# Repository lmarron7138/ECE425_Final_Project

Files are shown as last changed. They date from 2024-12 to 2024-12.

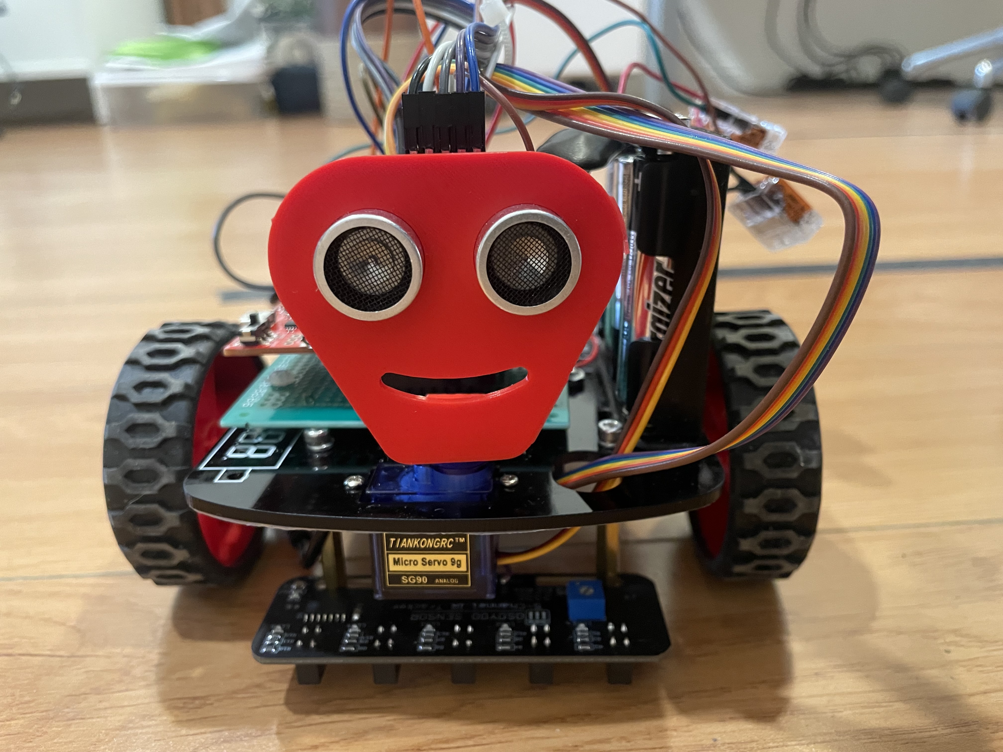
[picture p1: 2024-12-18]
Pictures/IMG_0241.JPG

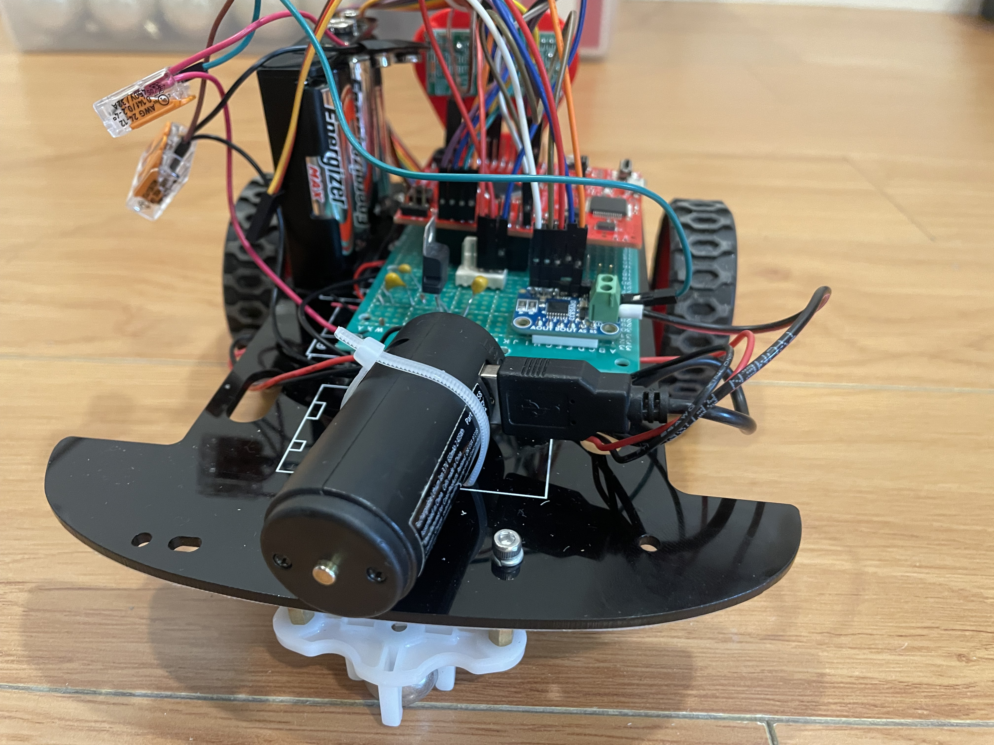
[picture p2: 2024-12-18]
Pictures/IMG_0248.JPG

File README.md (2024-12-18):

ECE 425 - Microprocessor Systems, Fall 2024

Final Project: Pathfinder Robot

Lenny Marron,
Roger Xu

Instructor: Aaron Nanas

## **<u>Introduction:</u>**

This project fulfills the final project requirement for the following
classes at California State University, Northridge (CSUN):

### **<u>Project Goals</u>**

To design and assemble a small robot that involves the use of an
ultrasonic sensor, and Two DC geared motors to give the robot the
ability to follow a specified path while avoiding
obstacles/obstructions. Using software written in C with Keil as the
development tool, the software instructions are sent to the TM4C123GXL
hardware board to process the data. This project explores data
transmission and communication protocols like UART, motor control with
PWM, Timer, and main microcontroller-peripherals interactions.

## **<u>Background and Methodology:</u>**

We used UART module 1 to transmit and receive the distance measured by
the ultrasonic sensor to the microcontroller and we used UART module 0
to allow us to view the data seen by the microcontroller. Once the data
was confirmed to be correct we then commented out the code relating to
UART module 0.

The DC motors were driven by the DRV8833 breakout board which used 4
separate PWM inputs to allow the robot to move forward, backward, left,
and right. We based our motor control using logic in **Table 1** below.

**<u>Table 1 Motor Control Logic</u>**



By using the DRV8833, it provided the ability to control 2 DC motors
with +3.3V input logic and a small footprint. The speed of the motors
was adjusted by changing the duty cycle of the PWM modules. When one
motor has a higher speed than the other, the car will turn in that
direction. When both motors have the same speed, the car will move
forward or backward.

Once the drivers for all 4 PWM signals and the 2 UART modules were
confirmed as working, a Timer Interrupt was created in order to
periodically check for any objects in front of the robots path. The
timer was set to count every 1 ms but would only check the distance in
front of it every 1 second. Whenever an object was less than 10 cm away
from the robot the robot would reverse and turn right, for all other
cases the robot would continue to drive forward.

We also 3D printed the ultrasonic sensor housing below in order to keep
the location of the US-100 sensor the same the entire time.

### **<u>CAD model of 3d Printed Parts</u>**

cad

## **<u>Block Diagram:</u>**



## **<u>Table of Components:</u>**

| **Part** | **QTY** | **Picture** |
|----|----|----|
| 5 Channel IR Tracking sensor module | 1 |  |
| DC Geared Motors with wires | 1 |  |
| Adafruit DRV8833 DC/Stepper Motor Driver Breakout Board | 1 |  |
| EK-TM4C123GXL microcontroller | 1 |  |
| US-100 Ultrasonic sensor | 1 |  |
| +6V (AA) battery Pack | 1 |  |
| +5V Coast Rechargeable Battery | 1 |  |

## 

## **<u>Pinout Table :</u>**

<table>
<colgroup>
<col style="width: 25%" />
<col style="width: 25%" />
<col style="width: 25%" />
<col style="width: 25%" />
</colgroup>
<thead>
<tr>
<th style="text-align: center;"><strong>EK-TM4C123GXL
Microcontroller</strong></th>
<th style="text-align: center;"><strong>Function Used</strong></th>
<th style="text-align: center;"><p><strong>DRV8833</strong></p>
<p><strong>Breakout Board</strong></p></th>
<th style="text-align: center;"><p><strong>US-100</strong></p>
<p><strong>Ultrasonic Sensor</strong></p></th>
</tr>
<tr>
<th style="text-align: center;">PB6</th>
<th style="text-align: center;"><p>PWM0_0</p>
<p>(Right motor forward)</p></th>
<th style="text-align: center;">BIN1</th>
<th style="text-align: center;"></th>
</tr>
<tr>
<th style="text-align: center;">PB4</th>
<th style="text-align: center;"><p>PWM0_1</p>
<p>(Right motor backward)</p></th>
<th style="text-align: center;">BIN2</th>
<th style="text-align: center;"></th>
</tr>
<tr>
<th style="text-align: center;">PF2</th>
<th style="text-align: center;"><p>PWM1_3</p>
<p>(Left motor forward)</p></th>
<th style="text-align: center;">AIN2</th>
<th style="text-align: center;"></th>
</tr>
<tr>
<th style="text-align: center;">PA6</th>
<th style="text-align: center;"><p>PWM1_1</p>
<p>(Left motor back)</p></th>
<th style="text-align: center;">AIN1</th>
<th style="text-align: center;"></th>
</tr>
<tr>
<th style="text-align: center;">PA0 (U0RX)</th>
<th style="text-align: center;">UART0</th>
<th style="text-align: center;"></th>
<th style="text-align: center;"></th>
</tr>
<tr>
<th style="text-align: center;">PA1 (U0TX)</th>
<th style="text-align: center;">UART0</th>
<th style="text-align: center;"></th>
<th style="text-align: center;"></th>
</tr>
<tr>
<th style="text-align: center;">PB0 (U1RX)</th>
<th style="text-align: center;">UART1</th>
<th style="text-align: center;"></th>
<th style="text-align: center;">Echo/RX pin 3</th>
</tr>
<tr>
<th style="text-align: center;">PB1 (U1TX)</th>
<th style="text-align: center;">UART1</th>
<th style="text-align: center;"></th>
<th style="text-align: center;">Trig/TX pin 2</th>
</tr>
</thead>
<tbody>
</tbody>
</table>

### **<u>Schematic:</u>**

()

## **<u>Analysis and Results :</u>**

One of the issues we ran into while working on this project was
implementing both the 5 channel IR tracking Sensors and the US-100
sensor at the same time. Although the interrupt function for the IR
sensor worked fine we always had errors when implementing both together.
Next time we will order an IR-sensor module that includes a datasheet
and comes from a reliable source. When troubleshooting this module using
a multimeter, we noticed the output voltages at ~ +1.7V when sensing the
black tape, which in turn caused the micro to read the input as a Logic
High, instead of Logic Low. We believe that if it weren’t due to the
lack of a datasheet we might have been able to fix this issue.

Another issue we faced is parsing the distance value measured by the
ultrasonic sensor to the microcontroller. We have had a lot of trouble
setting the microcontroller to measure the time it takes for the
ultrasonic sensor to receive its echo(which is how it measures
distance), we bypassed this issue by using UART as a communication
method instead of a direct pin connection. Aside from programming
obstacles, we have also experienced physical hardware roadblocks. The
ultrasonic sensor holder was not fitting properly, so we had to 3D print
new parts. However, despite all the setbacks, we were able to
successfully build a robot that scans its surroundings using sensors and
makes speed and direction changes based on its sensory inputs.

### **<u>Video Demonstration</u>**

Short video demonstration of collision avoidance:

- [<u>Video demo
  1</u>](https://drive.google.com/file/d/1N911rxExsTW1idhbEZjhIfGKM85qhewT/view?usp=drive_link)

- [<u>Video demo
  2</u>](https://drive.google.com/file/d/11KXWsSGZQswzX816z1DkIamCJ6btKC-2/view?usp=drive_link)

## **<u>Conclusion:</u>**

In conclusion, this project is the culmination of everything we have
learned in the class, from C programming to GPIO to GPTM to PWM to UART.
We connected different parts and peripherals to the microcontroller by
assigning and connecting them using GPIO pins. We applied communication
methods of UART to transfer distance data from the ultrasonic sensor to
the MCU by setting the appropriate baud rate. In addition we designed
the robot to periodically check its surroundings so as to not drain the
batteries as quickly. We learned how to use duty cycles to change the
speed of the motors by manipulating the duty cycle of the PWM, and thus
enabling us to adjust the speed of the motor. We also learned how to use
an H-bridge circuit to control the direction of our robot. We used
various C programming techniques to build up the control logic needed to
instruct the robot how to handle different situations. This project has
helped us gain a deeper understanding of MCUs and the crucial roles they
play in real life embedded systems.

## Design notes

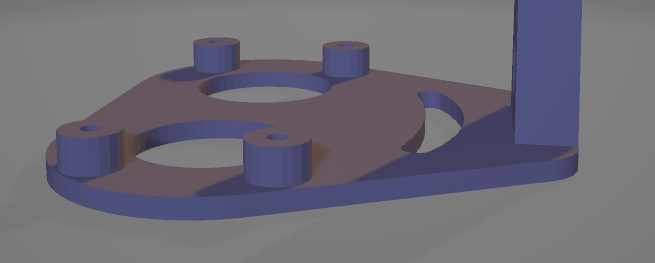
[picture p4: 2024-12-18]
3d_Models/Smiley Face ISO Left View.PNG

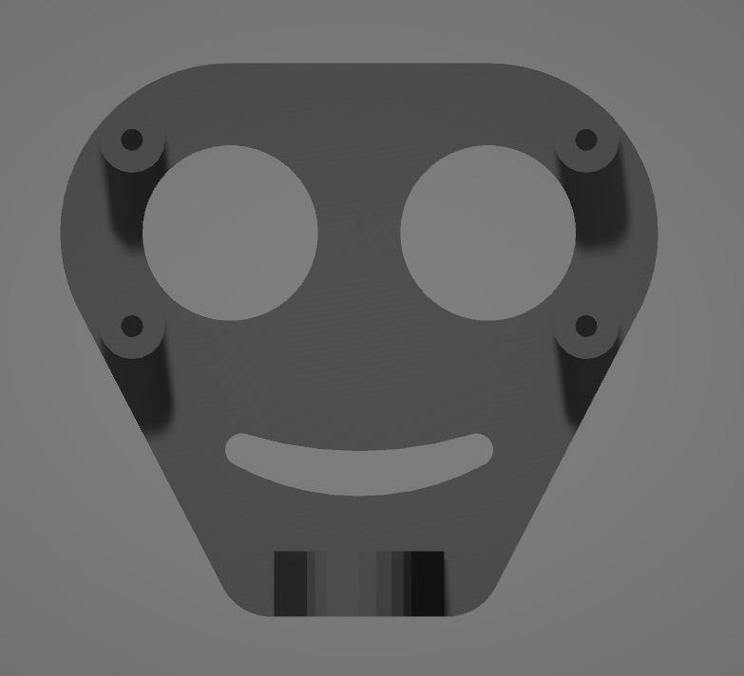
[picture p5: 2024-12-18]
3d_Models/Smiley Face Top View.PNG

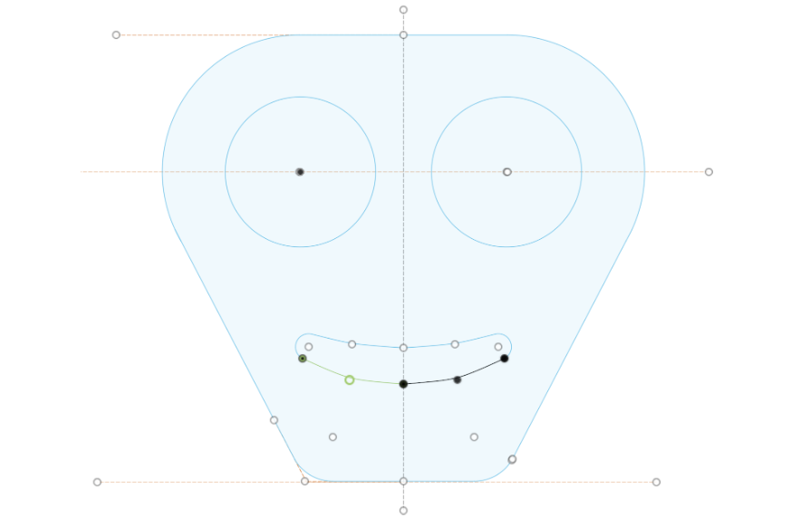
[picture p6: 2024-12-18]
3d_Models/Smiley Face Sketch.PNG

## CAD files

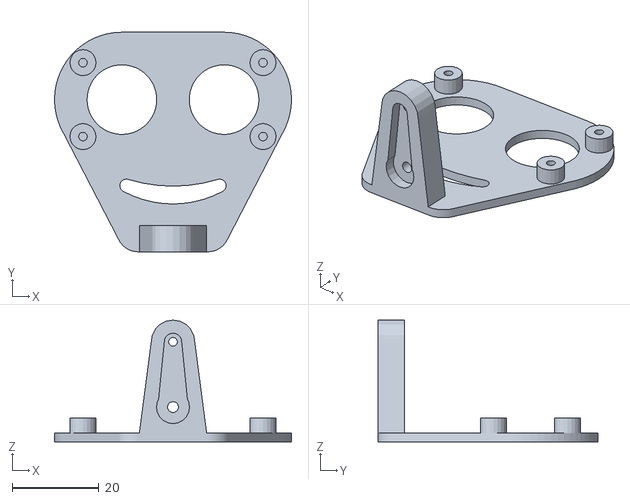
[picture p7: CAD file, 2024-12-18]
3d_Models/STL_Files/Smiley Face.stl
54.5 x 50.5 x 28.0

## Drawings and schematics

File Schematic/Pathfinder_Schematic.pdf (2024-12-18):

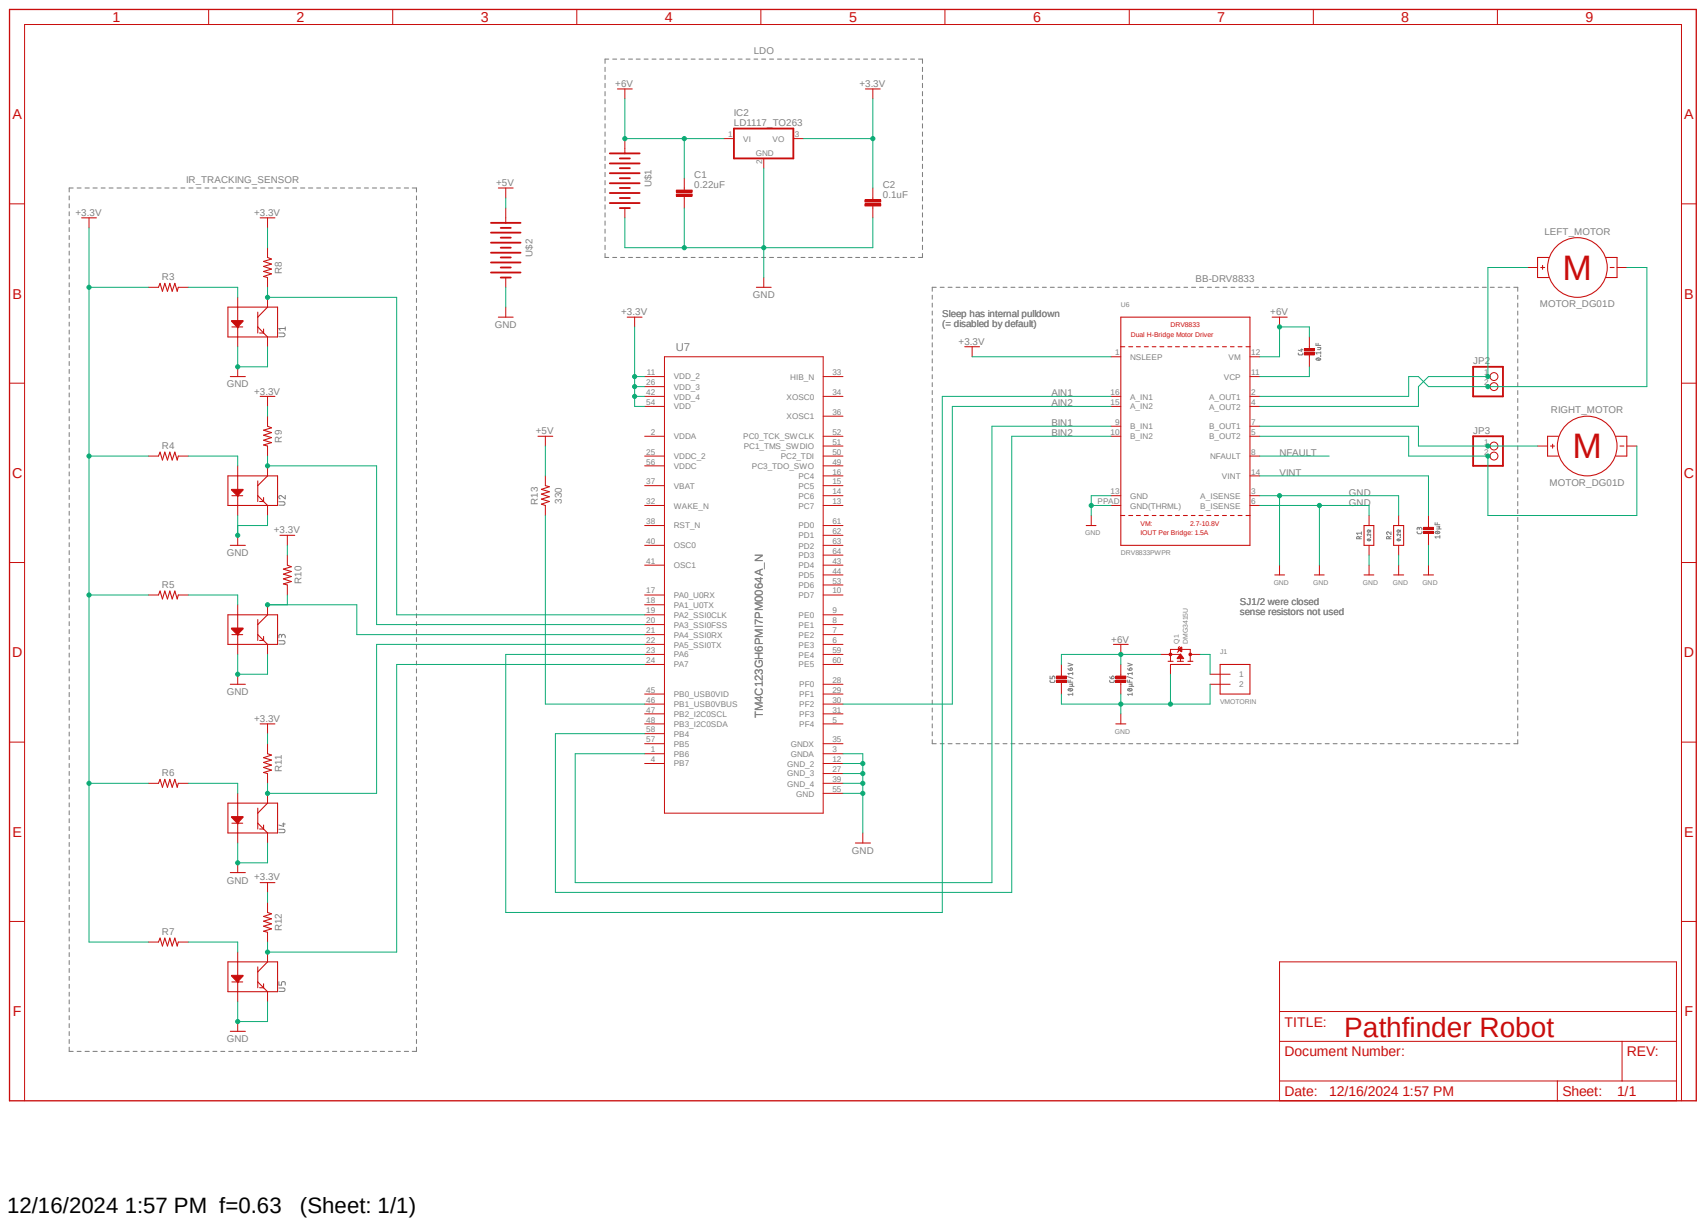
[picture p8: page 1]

Sleep has internal pulldown

SJ1/2 were closed
sense resistors not used

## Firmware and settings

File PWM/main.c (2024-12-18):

/*
 * @file main.c
 *
 * @brief Main source code for the Pathfinder Robot.
 *
 * This file contains the main entry point and function definitions for the Pathfinder Robot.
 * It Generates 4 PWM signals, a 1ms Timer interrupt, 9600 UART1 communication, SysTickTimer .
 *
 * Timer 0A generates periodic interrupts every 1 ms in order to count the 
 * amount of time needed to turn trigger the US-100 sensor and check obstacles in front of it. 
 *
 *
 * It interfaces with the following:
 *  - User LED (RGB) Tiva C Series TM4C123G LaunchPad
 *	- DRV8833 DC Motor Driver
 *	- SG90 Micro Servo Motor
 *	-	Two DC Motors Gearboxes 
 *				- Right motor controlled  PB6 (PWM0_0)FWD    PB4 (PWM0_1) REV
 *				- Left motor controlled   PF2 (PWM1_3)FWD    PA6 (PWM1_1) REV
 *
 *
 *	DRV8833 Breakout Board
 *  - DRV8833   (AIN1)  <-->  Tiva LaunchPad PA6
 *  - DRV8833   (AIN2)  <-->  Tiva LaunchPad PF2
 *  - DRV8833   (BIN1)  <-->  Tiva LaunchPad PB6
 *  - DRV8833   (BIN2)  <-->  Tiva LaunchPad PB4
 *  - DRV8833   (SLP)   <-->  +3.3V (Active High)
 *
 *  - DRV8833   (AOut1)<-->  DC Motor (+)
 *  - DRV8833   (AOut2)<-->  DC Motor (-)
 *  - DRV8833   (BOut2)<-->  DC Motor (-)
 *  - DRV8833   (BOut1)<-->  DC Motor (+)
 *
 *  - DRV8833   (VM+)  <-->  +6V (Battery Pack)
 *  - DRV8833   (VM-)  <-->  GND (Battery Pack)
 *
 * UART0 was used during the debugging
 * For PC communication using:
 *  - PA0 = UART0 RX
 *  - PA1 = UART0 TX
 *
 * The US-100 Ultrasonic Distance Sensor uses the following pinout:
 *  - US-100 Pin 1 (VCC)  <-->  Tiva LaunchPad 3.3V
 *  - US-100 Pin 2 (TX)   <-->  Tiva LaunchPad Pin PB1 (U1TX)
 *  - US-100 Pin 3 (RX)   <-->  Tiva LaunchPad Pin PB0 (U1RX)
 *  - US-100 Pin 4 (GND)  <-->  Tiva LaunchPad GND
 *  - US-100 Pin 5 (GND)  <-->  Tiva LaunchPad GND
 *
 *
 * @author Lenny Marron
 */
 

#include "TM4C123GH6PM.h"
#include "SysTick_Delay.h" 
#include "PWM_Clock.h"
#include "PWM0_0.h"
#include "PWM0_1.h"
#include "PWM1_1.h"
#include "PWM1_3.h"
#include "Motor_CTL.h"
#include "UART0.h"
#include "UART1.h"
#include "Timer_0A_Interrupt.h"
#include "IR_Tracking_Sensor_Interrupt.h"

#define BUFFER_SIZE   64
#define READ_DISTANCE 0x55

void Timer_0A_periodic_Task (void);
void IR_Sensor_Handler (uint8_t ir_sensor_status); //extern
static uint32_t Timer_0A_ms_elapsed= 0;
int Space  = 0;


int Distance_cm (void)
{
	char US_100_UART_Buffer[BUFFER_SIZE] = {0};
	
		UART1_Output_Character(READ_DISTANCE);
		
		US_100_UART_Buffer[0] = UART1_Input_Character();  //buffer aka read
		US_100_UART_Buffer[1] = UART1_Input_Character();
		
		uint16_t distance_value = ((US_100_UART_Buffer[1] | (US_100_UART_Buffer[0] << 8))/10);

	return distance_value ;
}



int main(void)
{
	//Used to Initialize Systick Timer blocking delay functions
	   SysTick_Delay_Init();
	
	// PWM clock divisor used to update clock to 3.125 MHz
	   PWM_Clock_Init();
	
	// Initializes PB and sets Period_Constant = 62500  
	   PWM0_0_Init(62500,0);  // works PB6
	
	// Initializes PB and sets Period_Constant = 62500  
     PWM0_1_Init(62500,0);  // works PB4
	
	// Initializes PB and sets Period_Constant = 62500   
     PWM1_1_Init(62500,0); // works PA6
	
	// Initializes PB and sets Period_Constant = 62500  
	   PWM1_3_Init(62500,0); // works PF2
	
	// Initialize the IR Channel Interrupts (Port A) 
	   //IR_Sensor_Interrupt_Init(&IR_Sensor_Handler); // working

  // Initialize the UART0 module which will be used to print characters on the serial terminal
	// UART0_Init();
	
	// Initialize the UART1 module which will be used to communicate with the US-100 Ultrasonic Distance Sensor
	   UART1_Init();
	
	// Initializes the Timer A0 Interrupts 
	   Timer_0A_Interrupt_Init (&Timer_0A_periodic_Task); //working
	
	while(1)
	{						
	    Move_FWD (0.3);
	}
}


// Timer will check distance every 1 seconds
void Timer_0A_periodic_Task (void)
{
	Timer_0A_ms_elapsed ++;
	
  if ((Timer_0A_ms_elapsed % 1000 ) == 0)
	{
	 Space = Distance_cm(); // measure distance infront
		 if (Space < 10)
		 {
			Move_Right (0.3);
			//SysTick_Delay1ms (200);
			 
			 // if (Space % 300)
			for (int i=0; i < 100; i++ )
			Move_REV ( .3 );    
     }
  }
}


/* 
******************************************
**  NOT WORKING WITH TIMER_0A and UART1 **
******************************************

// will decide where to shift the robot based off of IR input
void IR_Sensor_Handler (uint8_t ir_sensor_status)
{   
  switch (ir_sensor_status)
    { 
			//Not Reading Black REverse motors!!!
	    case 0xBC:
	    { 
				Move_REV (.4);	
				SysTick_Delay1ms (200);
				Move_Left (.4);
				SysTick_Delay1ms (200);
				
				break;
	    }
		
	    case 0x3C:	//IR5 (PA7) seeing black change Right motor 
	    { 
			 BREAK ();
		   PWM0_0_Update_Duty_Cycle (62500 * .4); // Right motor 30%
		   PWM1_3_Update_Duty_Cycle (62500 * .45);	// Left motor 40%
			 SysTick_Delay1ms (100);
	
		   break;
	    }
		
	    case 0x1C:	// IR5 (PA7) + IR4 (PA5) seeing black change Right motor by 35%
	    {
			 	 BREAK ();
		   PWM0_0_Update_Duty_Cycle (62500 * .4); // Right motor 30%
		   PWM1_3_Update_Duty_Cycle (62500 * .45);	// Left motor 40%
			 SysTick_Delay1ms (100);
			
			break;
	    }
			
	    case 0xB0://IR1 (PA2) + IR2 (PA3) seeing black change Left motor by 35%
	    { 
	     BREAK ();
				
		//			- Right motor controlled  PB6 (PWM0_0)FWD    PB4 (PWM0_1) REV
    //  		- Left motor controlled PF2 (PWM1_3)FWD    PA6 (PWM1_1) REV
				 
			 PWM0_0_Update_Duty_Cycle (62500 * .4);   // Right motor 30%
			 PWM1_3_Update_Duty_Cycle (62500 * .5);	// Left motor 35%	
			 SysTick_Delay1ms (100);
				
		   break;
	    }
			
	    case 0xB8: //IR1 (PA2) seeing black change Left side by % 15
	    {
	    BREAK ();

			PWM0_0_Update_Duty_Cycle (62500 * .4); //	Right motor 30%
			PWM1_3_Update_Duty_Cycle (62500 * .5);	// Left motor 40%	
			SysTick_Delay1ms (100);
		
		  break;
	    }
	default: //A4 & middle
	{
	   	  Move_FWD (0.4);
	break;
	}
 }
}

*/
		

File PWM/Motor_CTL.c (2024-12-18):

/**
 * @file Motor_CTL.c
 *
 * @brief Source file for the DRV8833 driver.
 *
 * This file contains the function definitions for the DRV8833 driver.
 * PWM signals with a DRV8833 breackout board	& Two DC GearMotors 
 *				- Right motor controlled  PB6 (PWM0_0)FWD    PB4 (PWM0_1) REV
 *				- Left motor controlled PF2 (PWM1_3)FWD    PA6 (PWM1_1) REV
 *
 * @note This driver assumes that the PWM_Clock_Init, PWM0_0_Init, PWM0_1_Init, PWM1_1_Init, and PWM1_3_Init 
 * functions have been called
 * 
 *
 * @author Lenny Marron
 */

#include "Motor_CTL.h"
#include "PWM_Clock.h"
#include "PWM0_0.h"
#include "PWM0_1.h"
#include "PWM1_3.h"
#include "PWM1_1.h"
#include "SysTick_Delay.h" 


/**
 * @brief  Adjusts PWM signals to allow FWD drive direction. 
 *
 * @param  PB6 (PWM0_0) PF2 pin (M1PWM6) are set to the minimum forward drive speed
 *				 While PB4 (PWM0_1) and PA6 (PWM1_1) are set to logic level LOW.
 *
 * @return None
 */
void Move_FWD (float power)
{
	BREAK ();	
	PWM0_0_Update_Duty_Cycle (62500 * power);
	PWM1_3_Update_Duty_Cycle ((62500 * power)+ 10000);//motor moves slower than the other side
}

/**
 * @brief  Adjusts PWM signals to allow Right drive direction. 
 *
 * @param  Stops right motor and continues with Left Motor speed to turn right.
 *				 PB6 (PWM0_0) is set to the minimum forward drive speed
 *				 PF2 pin (M1PWM6) PB4 (PWM0_1) and PA6 (PWM1_1) are set to logic level LOW.
 *
 * @return None
*/
void Move_Right (float power)
{
	BREAK ();	
	PWM1_3_Update_Duty_Cycle ((62500 * power)+ 10000);//motor moves slower than the other side

}

/**
 * @brief  Adjusts PWM signals to allow Left drive direction. 
 *
 * @param  Stops Left motor and continues with Right Motor speed to turn Left.
 *				 PF2 pin (PWM1_3) is set to the minimum forward drive speed
 *				 PB6 (PWM0_0)PB4 (PWM0_1) and PA6 (PWM1_1) are set to logic level LOW.
 *
 * @return None
*/
void Move_Left (float power)
{
	BREAK ();	
	PWM0_0_Update_Duty_Cycle (62500 * power); 
}



/**
 * @brief  Adjusts PWM signals to allow REV drive direction. 
 *
 * @param  PB4 (PWM0_1) and PA6 (PWM1_1) are set to the minimum forward drive speed
 *				 While PB6 (PWM0_0) PF2 pin (M1PWM6) are set to logic level LOW.
 *
 * @return None
 */
void Move_REV (float power)
{
	BREAK ();	
	PWM0_1_Update_Duty_Cycle (62500 * power); 
	PWM1_1_Update_Duty_Cycle (62500 * power); // 
}


/**
 * @brief  Adjusts PWM signals to allow motors to stop. 
 *
 * @param  All PWM signals are set to are set to logic level LOW.
 *					 PB4 (PWM0_1)  PA6 (PWM1_1) PB6 (PWM0_0) PF2 pin (M1PWM6) 
 *
 * @return None
 */
void BREAK (void)
{
	PWM0_0_Update_Duty_Cycle (0); 
	PWM0_1_Update_Duty_Cycle (0);	
	PWM1_1_Update_Duty_Cycle (0); 
	PWM1_3_Update_Duty_Cycle (0); 
}

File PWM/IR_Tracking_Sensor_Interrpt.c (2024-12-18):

/**
 * @file IR_Tracking_Sensor_Interrupt.h
 *
 * @brief Header file for the IR_Tracking_Sensor_Interrupt driver.
 *
 * This file contains the function definitions for the IR_Sensor_Interrupt driver.
 * It interfaces with the IR Tracking Sensor module. The following pins are used:
 * 	- IR1 (PA2)
 *	- IR2 (PA3)
 *	- IR3 (PA4)
 *	- IR4 (PA5)
 *  - IR5 (PA6)
 *
 * The sensor works as follows: 
 * black is active at LOW level and white is active at HIGH.
 * It configures the pins to trigger interrupts on rising edges. 
 * Each individual IR sensor operates in an active high configuration.
 *
 * @author Lenny Marron
 */
 
#include "IR_Tracking_Sensor_Interrupt.h"
 
// Declare pointer to the user-defined task
void (*IR_Sensor_Task)(uint8_t ir_sensor_state);

void IR_Sensor_Interrupt_Init(void(*task)(uint8_t))
{
	// Store the user-defined task function for use during interrupt handling
	IR_Sensor_Task = task;
	
	// Enable the clock to Port A by setting the
	// R0 bit (Bit 0) in the RCGCGPIO register
	SYSCTL->RCGCGPIO |= 0x01;
	
	// Configure the PA6, PA5, PA4, PA3, and PA2 pins as input
	// by clearing Bits 6 to 2 in the DIR register
	GPIOA->DIR &= ~0x7C;
	
	// Configure the PA6, PA5, PA4, PA3, and PA2 pins to function as
	// GPIO pins by clearing Bits 6 to 2 in the AFSEL register
	GPIOA->AFSEL &= ~0x7C;
	
	// Enable the digital functionality for the PA6, PA5, PA4, PA3, and PA2 pins
	// by setting Bits 6 to 2 in the DEN register
	GPIOA->DEN |= 0x7C;
	
	// Enable the weak pull-up resistor for the PA6, PA5, PA4, PA3, and PA2 pins
	// by setting Bits 6 to 2 in the PUR register
	GPIOA->PUR |= 0x7C;
	
	// Configure the PA6,PA5, PA4, PA3, and PA2 pins to detect edges
	// by clearing Bits 6 to 2 in the IS register
	GPIOA->IS &= ~0x7C;
	
	// Allow the GPIOIEV register to handle interrupt generation
	// and determine which edge to check for the PA6, PA5, PA4, PA3, and PA2 pins 
	// by clearing Bits 6 to 2 in the IBE register
	GPIOA->IBE &= ~0x7C;
	
	// Configure the PA6, PA5, PA4, PA3, and PA2 pins to detect
	// Falling edges by clearing Bits 6 to 2 in the IEV register
	// Falling edges on the corresponding pins will trigger interrupts
	GPIOA->IEV &=~ 0x7C;
	
	// Clear any existing interrupt flags on the PA6, PA5, PA4, PA3, and PA2 pins
	// by setting Bits 6 to 2 in the ICR register
	GPIOA->ICR |= 0x7C;
	
	// Allow the interrupts that are generated by the PA6, PA5, PA4, PA3, and PA2 pins
	// to be sent to the interrupt controller by setting
	// Bits 6 to 2 in the IM register
	GPIOA->IM |= 0x7C;
	

	// Clear the INTA field is for PORT A (Bits 7 to 5) of the IPR[0] register (PRI0)
	NVIC->IPR[0] &= ~0x000000E0;
	
	// Set the priority level of the interrupts to 3. 
	//Port A has an Interrupt Request (IRQ) number of 0
	NVIC->IPR[0] |= (3 << 5);
	
	// Enable IRQ 0 for GPIO Port A by setting Bit 0 in the ISER[0] register
	NVIC->ISER[0] |= (1 << 0);
}

uint8_t IR_Sensor_Read(void)
{
	// Declare a local variable to store the status of the IR_Sensor
	// Then, read the DATA register for Port A
	// A "0x7C" bit mask is used to capture only the pins used the IR_Sensor
	uint8_t ir_sensor_state = GPIOA->DATA & 0x7C;
	
	// Return the status of the PMOD BTN module
	return ir_sensor_state;
}

void GPIOA_Handler(void)
{
	// Check if an interrupt has been triggered by any of
	// the following pins: PA6, PA5, PA4, PA3, and PA2
	if (GPIOA->MIS & 0x7C)
	{
		// Execute the user-defined function
		(*IR_Sensor_Task)(IR_Sensor_Read());
		
		// Acknowledge the interrupt from any of the following pins: 
		// PA6, PA5, PA4, PA3, and PA2
		// Then clear by setting (bits 2-6)
		GPIOA->ICR |= 0x7C;
	}
}

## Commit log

2024-12-18 Added 3d Models
    [Smiley Face.stl]
2024-12-18 Added Schematics
